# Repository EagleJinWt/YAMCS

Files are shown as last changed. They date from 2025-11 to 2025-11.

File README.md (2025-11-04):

[中文版/Chinese Version](README_CN.md)

# Yet Another MultiColor Solution (For klipper 3D Printers)

**Status:** WIP / Early Concept  
**Goal:** Get the most out of existing parts without reinventing the wheel  

---

## Overview  

This project explores a *low-cost* and *modular* approach to multi-color 3D printing — without the need for expensive AMS systems or complex servo mechanisms.  

Instead of building a completely new multi-material system, the idea is to combine existing, reliable components and let **Klipper** handle the orchestration.  

Think of it as:  
> “Four extruders + one *smart buffer* = a functional multi-color system.”  

---

## Core Components  

| Component | Description |
|---|---|
| **Mainboard** | You don't need this if you board have 4 or more motor slot empty. But having them on a seperate board make things easier to matain. I chosed the Mellow Fly's Micro4, that's exactly what you need. |
| **Stepper Driver** | A4988 will work, but a TMC2209/2208 is recomended for easier configuration. Note: If you are using a board have integraded drivers, for e.g. the Micro4 I used, as the name suggests, drivers are integraded, don't buy extra drivers. |
| **Extruders** | Standard **BMG-style extruders** — one per filament channel |
| **Buffer Unit** | A **Mellow LLL buffer** (A reletively cheap one I found) |
| **Sensors** |  - One **filament sensor** per channel (Insert detection, for trigging the load process)<br> - One **filament sensor** on the toolhead (detection & timing). <br>*You don't need motion detection, regular ones with a microswitch will do it* |
| **Filament Cutter** | Optional, Recommended — Install for higher success rate during color switching. It is not necessary, tip-forming can work after good tuning. Check [Filamatrix](https://github.com/sorted01/Filametrix) if you are using StealthBurner |
| **MOSFETs (x2)** | Used to emulate button presses on the buffer’s control PCB. Anything like a **BSS138** should work, you don't need those heavy load one |
| **4-in-1-out-adapter** | The Bambulab one for P1 serires works best for me, in theory you can use any one that works, even the printed ones |

*No extra mounting hardware needed! It's all off-the-shelf parts so they mount as is!*

Although with that being said, you might still need some extra screws, nuts, etc. Here is some you might want to keep some stock on:

| Name | Description |
|---|---|
| **M3 T-nut** | For mounting the extruder & buffer. Some BMG units might not come with them. Though you should have some left when building the machine |
| **Heat Shrinking Tube** | Before the PCB design came out, or you just don't feel like spending more on a PCB, a heat shrinking tube will help a lot on insulating the MOSFET |

---

## Concept  

One day, I was thinking about adding a buffer to my 3D printer. Then it hit me: four extruders plus one buffer basically equals a perfect multi-color system. It’s simpler and more stable than the servo-based approach, and it solves all those annoying synchronization headaches. Honestly, you don’t even need me to say it—just look at what manufacturers like Bambulab, Creality, and others are doing, and you’ll see they’re basically using the same idea.

But in the DIY 3D printing community, as far as I know, the only one doing something like this is Box Turtle. The problem is, their setup is way too complicated: it uses a custom mainboard to drive those N20 motors and a ton of aluminum extrusion for the structure, which drives the cost way up. Of course, there’s a reason for that—they’re carrying four spools of filament on top.

My approach is different: let a dedicated filament storage box do the heavy lifting (I will include the one I used. It is simple, but make sure to check the README in the stl folder.), and then focus on the electronics and mechanics of the multi-color system itself.

You might be thinking, “Wait, isn’t this basically the MMU/ERCF idea?” True, but their designs are still way too complex—they use lead screws, linear rods, and even require servos. So you can think of my approach as a Box Turtle that runs on a regular Klipper board (no special brushed motor driver needed) and uses an off-the-shelf buffer—but without Box part.

---

## Buffer Klipper Intigration (Probalbly he most technical part of this project)
The Mellow LLL Filament buffer uses it's own controller, and cannot talk to klipper directly. However, it have two buttons that handles the manual "Feed" and "Retract" feature. We can use this feature to integrate it into Klipper. Since klipper/MCU-in-general can't control whether a pin can conduct with another pin, we can't simulate buttons on MCU. But we can use two mosfets, and it will perfectly simulate a "Button". Basically, a mosfet have 3 pins, a Gate(G), a Drain(D), and a Source(S). When a voltage higher than a certain threshold is applied between G and S, the D and S will conduct, exactly how buttons works, just in a controlled way. I might release a PCB for that, since leave the mosfet hanging in the air is not the best solution.

### Simplified Flow  
1. Identify the two physical buttons on the buffer PCB (`feed` / `retract`).  
2. Desolder or parallel-connect each to a MOSFET acting as a digital switch.  
3. Control the MOSFET gates using Klipper output pins (e.g. via `SET_PIN`).  
4. Klipper now “presses” the buttons for you — fully integrated.  

This keeps the buffer’s internal logic intact while giving Klipper total control.  

---

## Advantages  

- **Cost-effective:** Reuses existing extruders and components.  
- **Flexible:** Works with any number of filament channels (limited only by your setup).  
- **Klipper-native:** All logic and sequencing can live inside your Klipper macros, no ```/extra/whatever.py``` needed. 
- **Open idea:** Modular and adaptable — just build what you need.  

---

## Current Status  

This project is currently **in the concept/WIP stage**.  
Prototyping is ongoing, and the design may evolve.  

If you decide to try it out or improve upon the concept, please **open an Issue** or **submit a PR** — I’d love to see your version of it!  

---

## Philosophy  

> *“Don’t reinvent the wheel — make it spin smarter.”*  

This project aims to leverage existing, battle-tested parts in new ways rather than designing everything from scratch.  

If you believe in clever hacks and low-cost innovation, you’re in the right place. 

---

## To-Do

- Add Assembly Manual for Respooler  
- Test Macro & Config
- Publish Slicer Settings 

---

## Related link

[ClockWork 2 filament sensor](https://www.printables.com/model/292186-stealthburner-clockwork-2-filament-sensor)

[Mellow LLL Filament Buffer Item Page](https://es.aliexpress.com/item/1005007265643359.html)

[Spool holder & rewinder](stl/README.md)

---

**License:** MIT  
**Contributors:** You (hopefully!)

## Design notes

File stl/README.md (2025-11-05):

# Filament Storage Box with Passive Respool

- Orient parts as shown in picture
- Paint supports as shown in picture, if not generated
- They are oriented like this and need support is because this is the only way to make reliable , accurate holes (As we all know FDM 3D printers can make better holes in XY-Plane and not in Z-Plane)
- Alternatively, cut the models (The Base, The Idler Roller, and The O-Ring holder) by half, you can print them without support, just sacrifices some strength (Because of combining parts afterwards) and you save a few grams of filament
- 20% infill

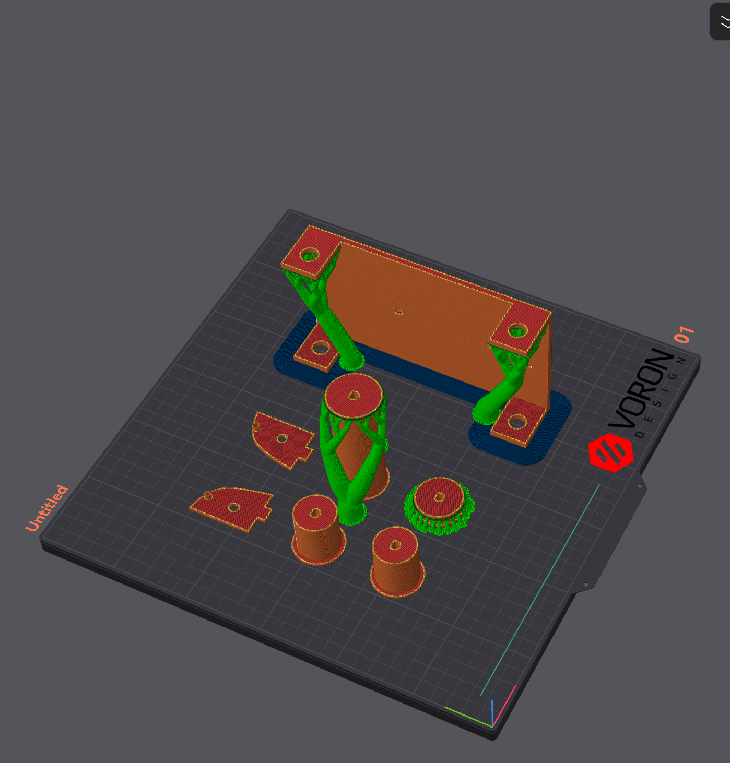
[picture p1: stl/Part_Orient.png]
Parts Orientation & Support


## BOM:

| Name | Quantity | Specifications |
|---|---|---|
| MR105 Bearing  | 4 per channel | |
| MR83 Bearing | 1 per channel | |
| M3x12 Screw | 1 per channel | |
| D-shaped shaft | 2 per channel | 90mm length |
| O-Ring | 2 per channel | 30mm outer diameter, 3mm width  |
| Rubber tube | ~ | 30mm outer diameter, 27mm inner |
| M4x10 Screw | 8 | |
| M4 Hex Nut | 8 | |
| M3 Hex Nut | 1 per channel | |
| Storage Box | 1 | L40.5, W31.5, H23(cm), Sealed |

### Note:
- **Buy extra** for the hardware listed above. Screws are usually sold in a pack of 25/50/100, so no worries on that
- The quantity for the rubber tube is not specified, since they are usually sold in meters, and 1 meter will be plenty
- For the o-ring, diameter don't have to be percise since they are flexible, but don't go too far off. The width matters, because that effects how hard it can grip the filament
- For the Rubber tube, diameter don't have to be percise since they are flexible, but don't go too far off
- The box size is for a 4-channel build, try to get the boxes without handle, because they conflicts with the filament spool sometimes
- Maybe considering buying some desiccant, since this is supposed to be a storage box

### Box Modification:
- 2 drilled holes per channel
- You can use the holes on the base plate as a jig
- Use a 5mm drill bit

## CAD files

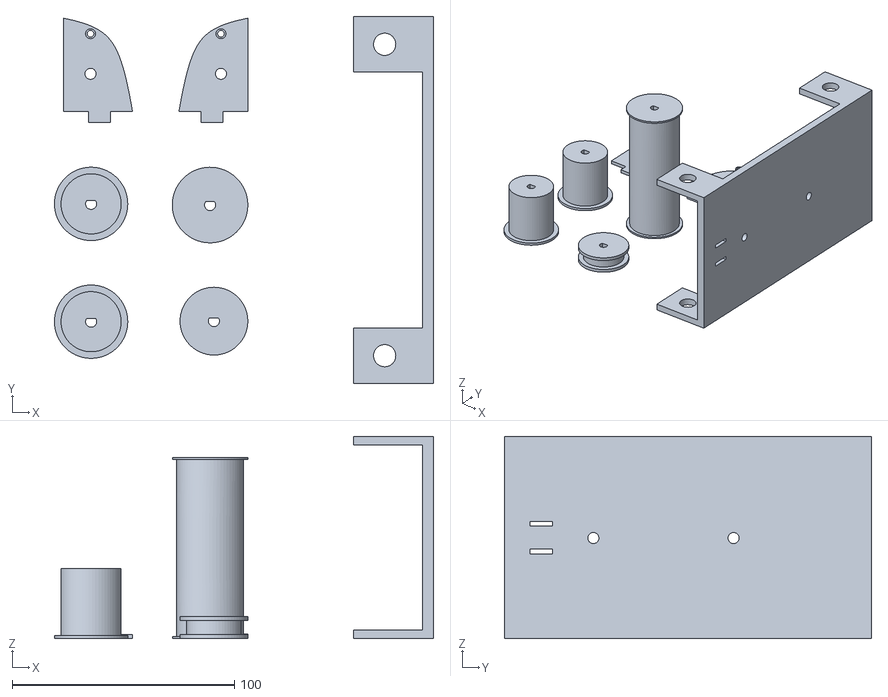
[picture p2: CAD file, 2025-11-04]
stl/AllThings_Print_One_Each_Channel.stl
170.5 x 165.0 x 91.0

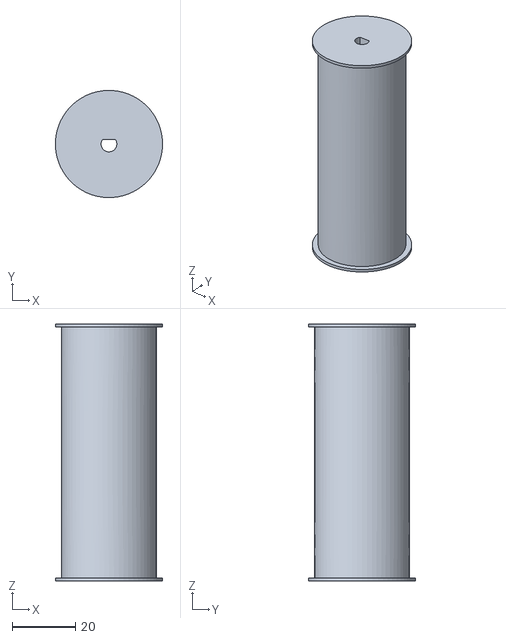
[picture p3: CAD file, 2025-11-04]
stl/Separated/Respooler Beta v2 v2.stl_3.stl
34.0 x 34.0 x 81.5

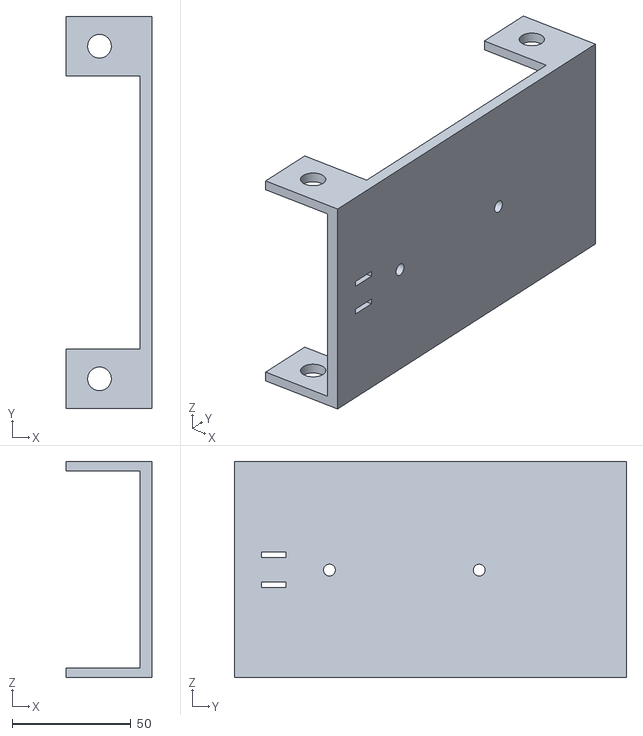
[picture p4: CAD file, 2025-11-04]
stl/Separated/Respooler Beta v2 v2.stl_2.stl
36.0 x 165.0 x 91.0

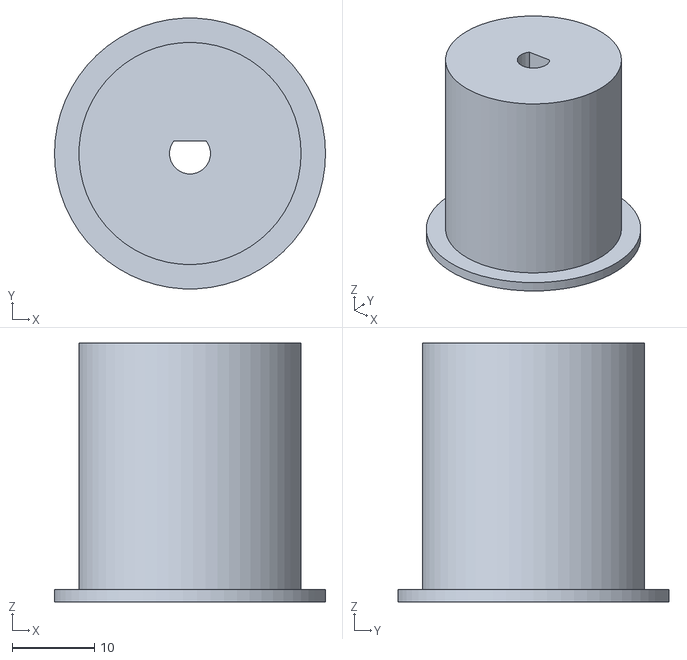
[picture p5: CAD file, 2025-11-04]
stl/Separated/Respooler Beta v2 v2.stl_5.stl
33.0 x 33.0 x 31.5

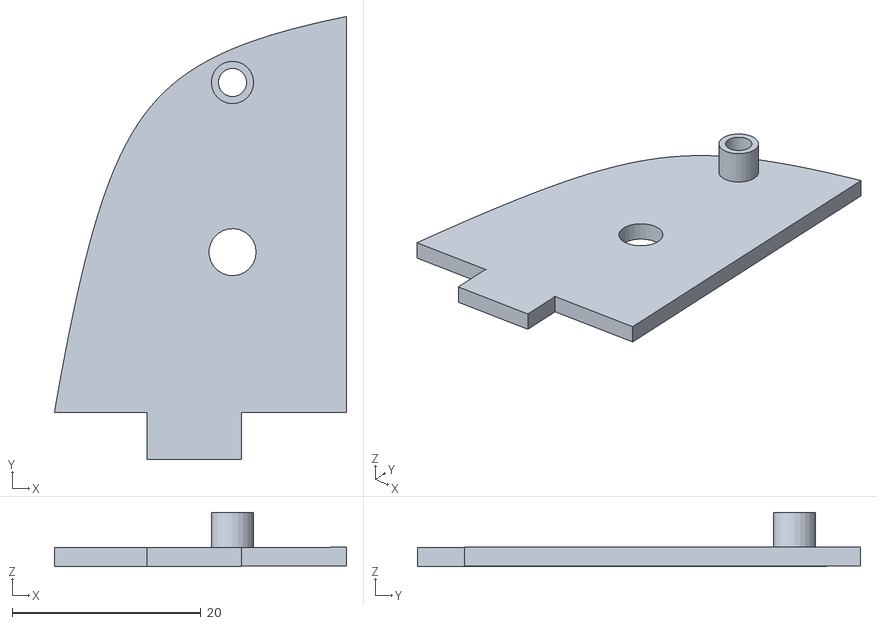
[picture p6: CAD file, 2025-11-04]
stl/Separated/Respooler Beta v2 v2.stl_6.stl
31.0 x 47.0 x 5.73

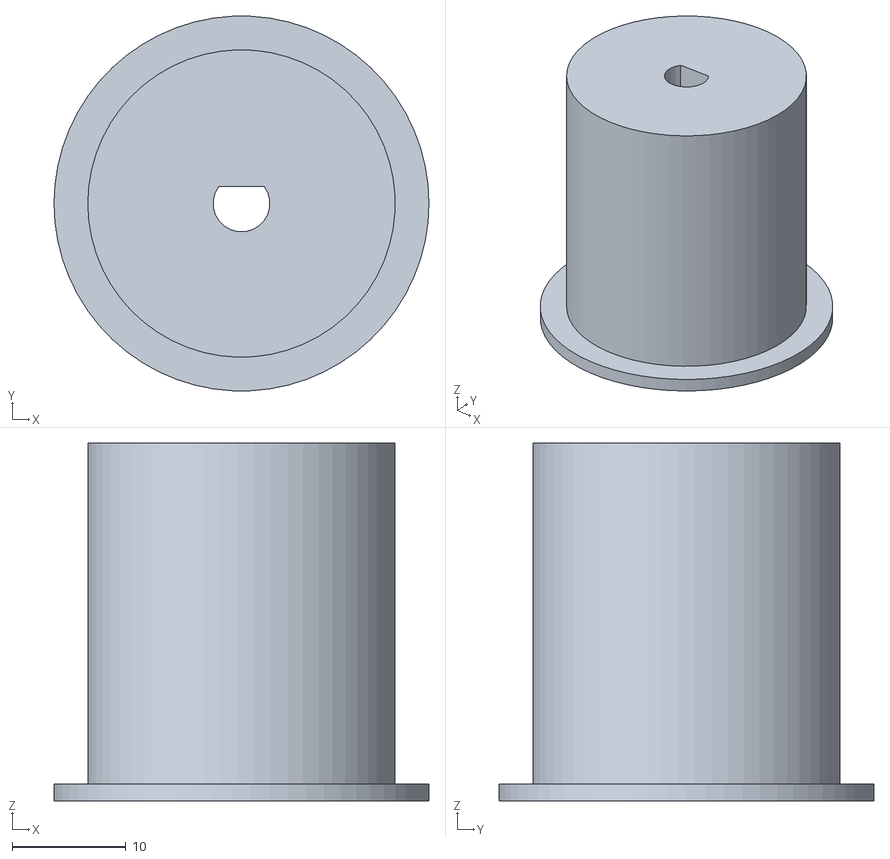
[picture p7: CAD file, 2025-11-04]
stl/Separated/Respooler Beta v2 v2.stl_4.stl
33.0 x 33.0 x 31.5

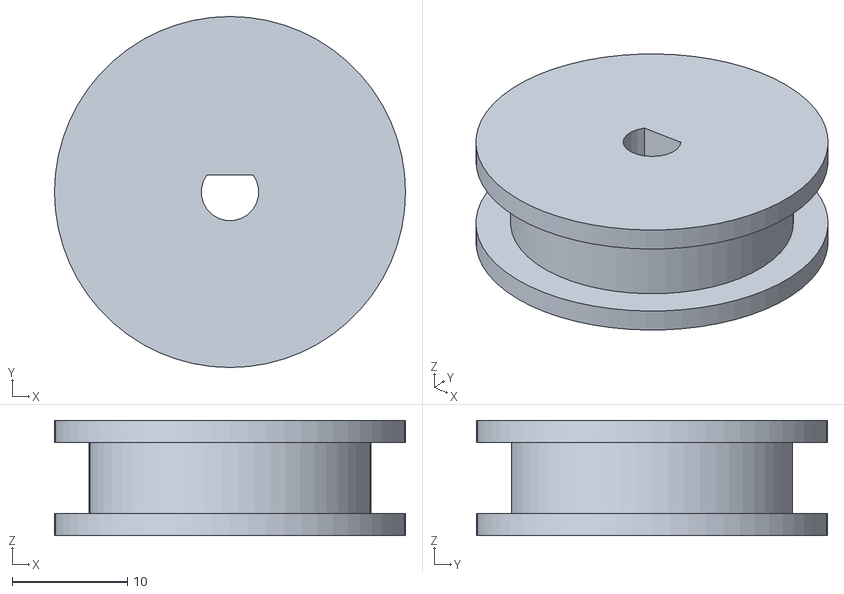
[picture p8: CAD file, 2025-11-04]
stl/Separated/Respooler Beta v2 v2.stl_1.stl
30.5 x 30.5 x 10.0

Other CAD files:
stl/Separated/Respooler Beta v2 v2.stl_7.stl
Respooler Beta v2.f3d

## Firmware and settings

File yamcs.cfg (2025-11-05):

# YAMCS Sample Config - 4 Channel
# NOTE: All pins, serials, and distances are placeholders. Update them before use.
# This configuration is not tested yet, use it on your own risk. (Although it is likely nobody will see this repo at all...)

[mcu YAMCS]
# MCU configuration plceholder for YAMCS board
serial: /dev/serial/by-id/usb-1a86_USB2.0-Serial-if00-port0

[extruder_stepper Channel0]
# Configuration for Channel 0 stepper motor
# NOTE: Update pin assignments and parameters as needed.
extruder: #Leave this blank!
step_pin: YAMCS:gpio6
dir_pin: YAMCS:gpio3
enable_pin: YAMCS:!gpio7
microsteps: 16
gear_ratio: 50:17 # BMG Gears
rotation_distance: 23.520

[tmc2209 extruder_stepper Channel0]
# TMC2209 driver settings for Channel 0
uart_pin: YAMCS:gpio9
uart_address: 0
interpolate: False
run_current: 0.8
sense_resistor: 0.110
stealthchop_threshold: 0

[extruder_stepper Channel1]
# Configuration for Channel 1 stepper motor
# NOTE: Update pin assignments and parameters as needed.
extruder: #Leave this blank!
step_pin: YAMCS:gpio6
dir_pin: YAMCS:gpio3
enable_pin: YAMCS:!gpio7
microsteps: 16
gear_ratio: 50:17 # BMG Gears
rotation_distance: 23.520

[tmc2209 extruder_stepper Channel1]
# TMC2209 driver settings for Channel 1
uart_pin: YAMCS:gpio9
uart_address: 1
interpolate: False
run_current: 0.8
sense_resistor: 0.110
stealthchop_threshold: 0


[extruder_stepper Channel2]
# Configuration for Channel 2 stepper motor
# NOTE: Update pin assignments and parameters as needed.
extruder: #Leave this blank!
step_pin: YAMCS:gpio6
dir_pin: YAMCS:gpio3
enable_pin: YAMCS:!gpio7
microsteps: 16
gear_ratio: 50:17 # BMG Gears
rotation_distance: 23.520

[tmc2209 extruder_stepper Channel2]
# TMC2209 driver settings for Channel 2
uart_pin: YAMCS:gpio9
uart_address: 2
interpolate: False
run_current: 0.8
sense_resistor: 0.110
stealthchop_threshold: 0

[extruder_stepper Channel3]
# Configuration for Channel 3 stepper motor
# NOTE: Update pin assignments and parameters as needed.
extruder: #Leave this blank!
step_pin: YAMCS:gpio6
dir_pin: YAMCS:gpio3
enable_pin: YAMCS:!gpio7
microsteps: 16
gear_ratio: 50:17 # BMG Gears
rotation_distance: 23.520

[tmc2209 extruder_stepper Channel3]
# TMC2209 driver settings for Channel 3
uart_pin: YAMCS:gpio9
uart_address: 3
interpolate: False
run_current: 0.8
sense_resistor: 0.110
stealthchop_threshold: 0

[filament_switch_sensor Channel0]
# Filament sensor for Channel 0
switch_pin: YAMCS:gpio12
pause_on_runout: False
insert_gcode:
  INITIAL_LOAD CHANNEL=0
  
[filament_switch_sensor Channel1]
# Filament sensor for Channel 1
switch_pin: YAMCS:gpio13
pause_on_runout: False
insert_gcode:
  INITIAL_LOAD CHANNEL=1
  
[filament_switch_sensor Channel2]
# Filament sensor for Channel 2
switch_pin: YAMCS:gpio14
pause_on_runout: False
insert_gcode:
  INITIAL_LOAD CHANNEL=2
  
[filament_switch_sensor Channel3]
# Filament sensor for Channel 3
switch_pin: YAMCS:gpio15
pause_on_runout: False
insert_gcode:
  INITIAL_LOAD CHANNEL=3

[filament_switch_sensor Buffer_Sensor]
# Buffer sensor to detect filament arrival
switch_pin: YAMCS:gpio18
pause_on_runout: True

[filament_switch_sensor Head_Sensor]
# Head sensor to detect filament at the toolhead
switch_pin: SB2040:gpio20
pause_on_runout: True

[output_pin Buffer_Push]
# Output pin for buffer "PUSH" button
pin: YAMCS:gpio10 #Pin of the mosfet corresponding to the "PUSH" button

[output_pin Buffer_Retract]
# Output pin for buffer "RETRACT" button
pin: YAMCS:gpio11 #Pin of the mosfet corresponding to the "RETRACT" button

[save_variables]
# Save variables to a file for persistent storage
filename: ~/printer_data/config/variables.cfg

[delayed_gcode STARTUP_SETUP]
# Startup setup to initialize slot and check filament status
initial_duration: 1
gcode:
  {% set svv = printer.save_variables.variables %}
  {% set all_sensors = [
    printer.filament_switch_sensor.Channel0.filament_detected,
    printer.filament_switch_sensor.Channel1.filament_detected,
    printer.filament_switch_sensor.Channel2.filament_detected,
    printer.filament_switch_sensor.Channel3.filament_detected
  ] %}
  {% set all_empty = all(v == False for v in all_sensors) %}

  {% if 'slot' not in svv %}
    RESPOND PREFIX="warn" MSG="No slot info found — initializing default slot 0."
    SAVE_VARIABLE VARIABLE=slot VALUE=0
  {% elif svv.slot not in [0,1,2,3] %}
    {action_emergency_stop("CRITICAL: Slot variable corrupted! Manual confirmation required.")}
  {% elif all_empty %}
    M117 "All slots empty, insert filament before printing."
    M118 "All slots empty, insert filament before printing."
  {% else %}
    T{svv.slot}
  {% endif %}

[gcode_macro INITIAL_LOAD]
# Macro to load filament from a specified channel
gcode:
  {% set channel = params.CHANNEL|int %}
  {% set safe_distance = 300 %}
  
  M118 "Loading From Channel{channel} ..."
  T{channel}
  SYNC_EXTRUDER_MOTION EXTRUDER=Channel{channel} MOTION_QUEUE=extruder
  {% while safe_distance > 0 %}
    SET_PIN PIN=Buffer_Push VALUE=1
    G1 E5 F600
    SET_PIN PIN=Buffer_Push VALUE=0
    {% set safe_distance = safe_distance - 5 %}
    G4 P300
    {% if printer.filament_switch_sensor.buffer_sensor.filament_detected %}
        M118 "Filament Arrived at buffer"
        {% break %}
    {% endif %}
  {% endwhile %}
  {% if safe_distance <= 0 %}
      {action_emergency_stop("Error! Buffer sensor not triggered over 300mm of push!")}
  {% else %}
      M118 "Channel {channel} loaded! Pushed {300-safe_distance}mm"
      SET_PIN PIN=Buffer_Retract VALUE=1
      G1 E-45 F600
      SET_PIN PIN=Buffer_Retract VALUE=0
  {% endif %}

[gcode_macro COLOR_CHANGE_LOAD]
# Macro to load filament during a color change
gcode:
  {% set channel = params.CHANNEL|int %}
  {% set safe_distance_toBuffer = 300 %}
  {% set safe_distance_toHead = 150 %}
  
  M118 "Loading From Channel{channel} ..."
  T{channel}
  SYNC_EXTRUDER_MOTION EXTRUDER=Channel{channel} MOTION_QUEUE=extruder
  {% while safe_distance_toBuffer > 0 %}
    SET_PIN PIN=Buffer_Push VALUE=1
    G1 E5 F600
    SET_PIN PIN=Buffer_Push VALUE=0
    {% set safe_distance_toBuffer = safe_distance_toBuffer - 5 %}
    G4 P300
    {% if printer.filament_switch_sensor.buffer_sensor.filament_detected %}
        M118 "Filament Arrived at buffer."
        {% break %}
    {% endif %}
  {% endwhile %}
  {% if safe_distance_toBuffer <= 0 %}
    PAUSE
    M118 Error! Buffer Sensor not triggered after {safe_distance_toBuffer}mm of push!
  {% endif %}
  {% while safe_distance_toHead > 0 %}
    SET_PIN PIN=Buffer_Push VALUE=1
    G1 E1 F600
    SET_PIN PIN=Buffer_Push VALUE=0
    {% set safe_distance_toHead = safe_distance_toHead - 1 %}
    G4 P300
    {% if printer.filament_switch_sensor.head_sensor.filament_detected %}
        M118 "Filament Arrived at Head."
        {% break %}
    {% endif %}
  {% endwhile %}
  {% if safe_distance_toHead <= 0 %}
      PAUSE
      M118 Error! Toolhead Sensor not triggered after {safe_distance_toHead}mm of push!
  {% else %}
      M118 "Channel {channel} loaded!"
  {% endif %}

[gcode_macro T0]
# Macro to select Channel 0
gcode:
  SYNC_EXTRUDER_MOTION EXTRUDER=Channel0 MOTION_QUEUE=extruder
  {% for n in [1,2,3] %}
    SYNC_EXTRUDER_MOTION EXTRUDER=Channel{{n}} MOTION_QUEUE=
  {% endfor %}
  SAVE_VARIABLE VARIABLE=slot VALUE=0
  
[gcode_macro T1]
# Macro to select Channel 1
gcode:
  SYNC_EXTRUDER_MOTION EXTRUDER=Channel1 MOTION_QUEUE=extruder
  {% for n in [0,2,3] %}
    SYNC_EXTRUDER_MOTION EXTRUDER=Channel{{n}} MOTION_QUEUE=
  {% endfor %}
  SAVE_VARIABLE VARIABLE=slot VALUE=1
  
[gcode_macro T2]
# Macro to select Channel 2
gcode:
  SYNC_EXTRUDER_MOTION EXTRUDER=Channel2 MOTION_QUEUE=extruder
  {% for n in [0,1,3] %}
    SYNC_EXTRUDER_MOTION EXTRUDER=Channel{{n}} MOTION_QUEUE=
  {% endfor %}
  SAVE_VARIABLE VARIABLE=slot VALUE=2
  
[gcode_macro T3]
# Macro to select Channel 3
gcode:
  SYNC_EXTRUDER_MOTION EXTRUDER=Channel3 MOTION_QUEUE=extruder
  {% for n in [0,1,2] %}
    SYNC_EXTRUDER_MOTION EXTRUDER=Channel{{n}} MOTION_QUEUE=
  {% endfor %}
  SAVE_VARIABLE VARIABLE=slot VALUE=3

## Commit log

2025-10-19 Revise README with detailed project information
    Expanded project overview and details on integration with Klipper. Added sections on advantages, current status, philosophy, and future plans.
2025-10-19 Fix spelling and formatting in README.md
    Corrected spelling and formatting issues in the Buffer Klipper Integration section.
2025-10-19 Update README with mounting hardware information
    Added note about mounting hardware being off-the-shelf.
2025-10-19 Fix typo in README about mounting hardware
2025-10-19 Refine component descriptions in README
    Updated descriptions for extruders and buffer unit in README.
2025-10-19 Revise README with component details and links
    Updated the README with detailed descriptions of components and their requirements. Added related links and clarified integration instructions for the Mellow LLL Filament buffer.
2025-10-19 Add Mellow LLL Filament Buffer link to README
2025-10-19 Update sensor description formatting in README
    Added emphasis to the sensor description in README.
2025-10-19 Update sensor descriptions in README.md
2025-10-19 Fix formatting of sensors section in README.md
2025-10-20 Clarify filament storage box approach in README
    Updated the README to clarify the filament storage box approach and added a link for the spool holder.
2025-10-20 Revise filament storage box description in README
    Updated the explanation of the filament storage box and added a note to check the README in the STL folder.
2025-10-20 Fix typo in filament storage box description
    Corrected a typo in the README regarding the filament storage box description.
2025-10-23 Revise README with BOM for Filament Storage Box
    Updated the README to provide detailed BOM for the Filament Storage Box design.
2025-10-23 Create yamcs.cfg with sample configuration
    Added a sample configuration file for YAMCS with multiple channels and settings.
    [yamcs.cfg]
2025-10-24 Update D-shaped shaft length and fix typo
    Corrected the length of the D-shaped shaft from 110mm to 90mm and fixed a typo in the note about the rubber tube diameter.
2025-10-24 Fix rubber tube inner diameter in README
    Updated the inner diameter of the rubber tube from 25mm to 27mm.
2025-10-24 Modify filament switch sensors and add macros
    Updated filament switch sensor configurations and added new macros for loading from the box and extruder synchronization.
    [yamcs.cfg]
2025-10-28 Modify slot initialization message and add macros
    Updated warning message for slot initialization and added new macros for loading filament and handling color changes.
    [yamcs.cfg]
2025-10-29 Update filament switch sensor configurations
    Replaced 'LOAD_FROM_BOX' with 'INITIAL_LOAD' for filament switch sensors and added a new sensor configuration for 'Head_Sensor'.
    [yamcs.cfg]
2025-10-29 Add notes, and simplify T macro logic
    [yamcs.cfg]
2025-10-29 Unify Channel Numbering
    [yamcs.cfg]
2025-10-29 Fix typo and missing endif
    [yamcs.cfg]
2025-11-01 Added Respoller CAD
    [Respooler Beta v2.f3d, Respooler Beta v2.step]
2025-11-01 Update M3 screw specification from M3x8 to M3x12
2025-11-01 Fix typo in filament cutter recommendation
2025-11-01 Fix Roller Spacing
    [Respooler Beta v2.f3d]
2025-11-04 Update STLs with updated design
    [AllThings_Print_One_Each_Channel.stl, Base.stl, Idler.stl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]
2025-11-04 Update CAD
    [Respooler Beta v2.f3d]
2025-11-04 Update README with printing instructions and alternatives
    Clarified instructions on part orientation and support requirements, and added an alternative printing method.
2025-11-04 Revise manufacturer names in design philosophy
    Updated references to 3D printing manufacturers in the design philosophy section.
2025-11-04 Update assembly manual tasks in README_CN.md
2025-11-05 Clarify descriptions in README_CN.md
    修正了README_CN.md中关于龟盒和缓冲器的描述，使其更加清晰和准确。
2025-11-05 Update warning message in yamcs.cfg
    [yamcs.cfg]
